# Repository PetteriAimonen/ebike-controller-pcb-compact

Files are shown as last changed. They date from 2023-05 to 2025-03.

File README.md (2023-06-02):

Custom E-bike controller based on VESC 4.10
===========================================

Customized version of [Benjamin Vedder's VESC](https://github.com/vedderb/bldc-hardware) for driving BLDC motors.

VESC Hardware is licensed under the Creative Commons Attribution-ShareAlike 4.0 International License. To view a copy of this license, visit http://creativecommons.org/licenses/by-sa/4.0/.

Can use either VESC firmware or my [custom firmware](https://github.com/PetteriAimonen/ebike-controller/).

Changes:

* Added screw terminals for power cables and 2.54 mm pin headers for signals.
* Most parts are on single-side, with parts available on JLCPCB.
* Added LSM6DS3 accelerometer on board for controlling assist power
* Designed for max. 20A 50V operation.

[Schematic](design/images/BLDC_4.pdf)

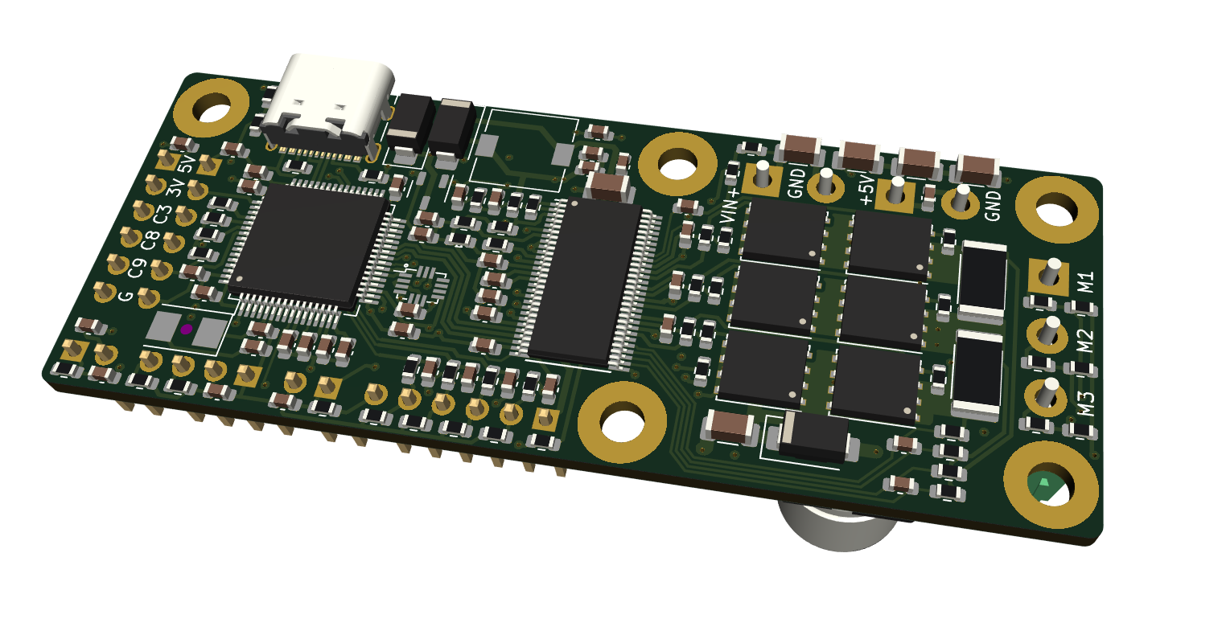
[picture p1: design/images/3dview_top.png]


Designed to mount on an aluminum block for cooling the FETs.
Alternatively a heatsink can be screwed on.

Assembly costs for 5 pcs at JLCPCB as of 2023:

    PCB (with 1 oz inner layer copper and lead-free HASL): $28.00
    Setup fee:$7.88
    Stencil:$1.48
    Components:$97.77
    Extended components fee:$29.56
    SMT Assembly:$3.43

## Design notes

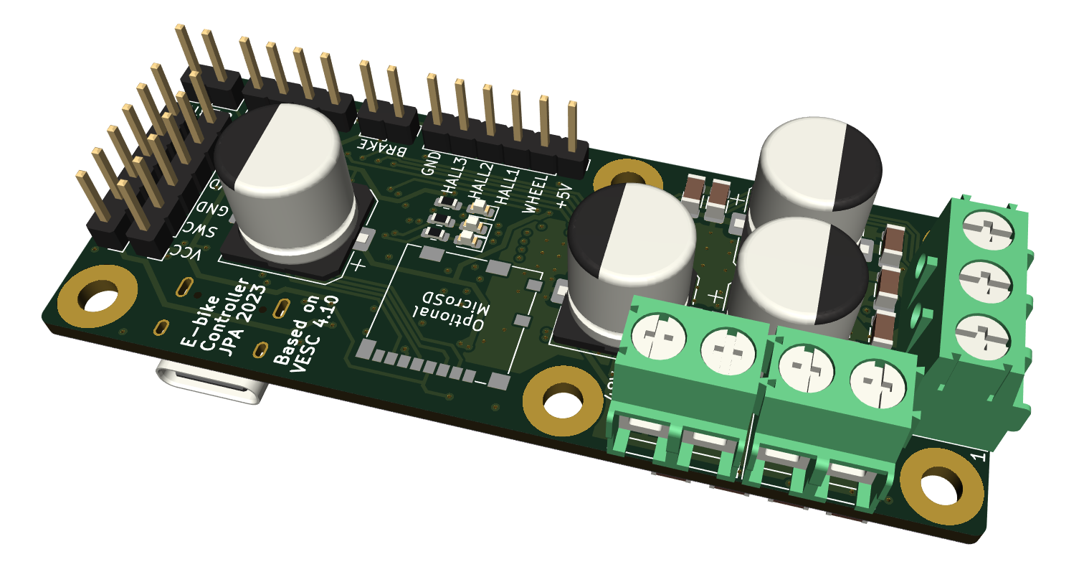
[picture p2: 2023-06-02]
design/images/3dview_bottom.png

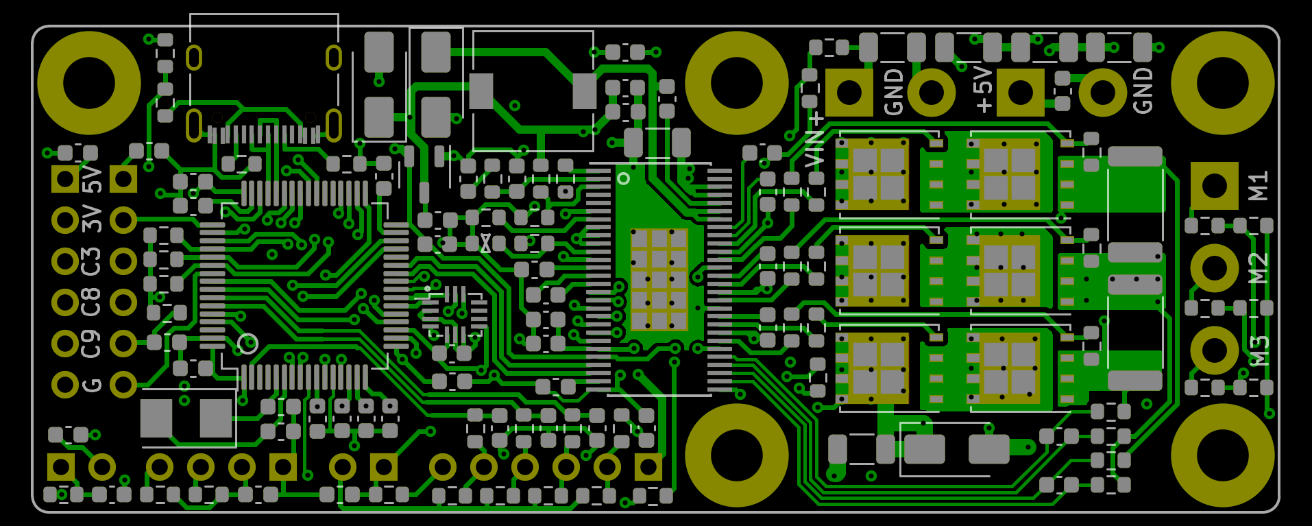
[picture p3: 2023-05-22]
design/images/BLDC_4_top.png

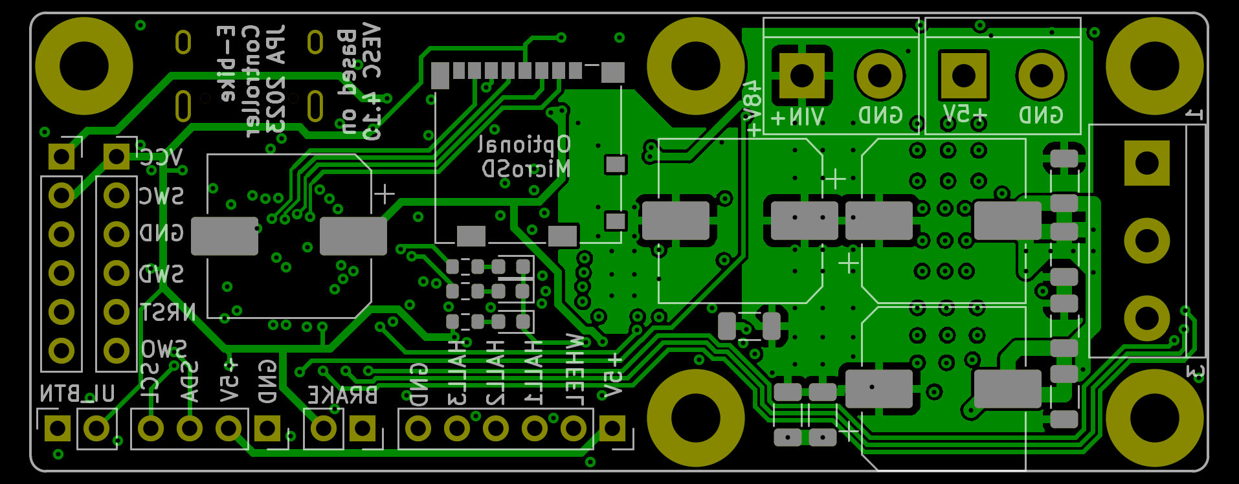
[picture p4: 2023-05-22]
design/images/BLDC_4_bottom.png

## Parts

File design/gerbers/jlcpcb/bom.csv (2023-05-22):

Comment | Designator | Footprint | LCSC
HALL/Encoder | P1 | Connector_PinHeader_2.54mm:PinHeader_1x06_P2.54mm_Vertical | N/A
100nF | C2,C11,C12,C13,C22,C27,C28,C29,C30,C32,C41,C42,C45,C62 | Capacitor_SMD:C_0603_1608Metric | C14663
2k2 | R4,R7,R11,R12,R13,R14,R15,R16,R18,R22,R24,R27,R31,R33 | Resistor_SMD:R_0603_1608Metric | C4190
39k | R3,R23,R26,R30,R32,R36,R46 | Resistor_SMD:R_0603_1608Metric | C23153
5m | R53,R54 | Resistor_SMD:R_2512_6332Metric | C5154719
100R | R37,R38,R48,R49,R50,R51 | Resistor_SMD:R_0603_1608Metric | C22775
RED | D2 | LED_SMD:LED_0603_1608Metric | N/A
GREEN | D1 | LED_SMD:LED_0603_1608Metric | N/A
LED | D3 | LED_SMD:LED_0603_1608Metric | N/A
40V_IN | J3 | TerminalBlock:TerminalBlock_bornier-2_P5.08mm | N/A
100uF,63V | C57,C58,C59 | Capacitor_SMD:CP_Elec_10x10.5 | N/A
Motor | J1 | TerminalBlock:TerminalBlock_bornier-3_P5.08mm | N/A
5V_OUT | J2 | TerminalBlock:TerminalBlock_bornier-2_P5.08mm | N/A
Schottky | D4 | Diode_SMD:D_SMA | C14996
DRV8302 | U3 | Package_SO:HTSSOP-56-1EP_6.1x14mm_P0.5mm_EP3.61x6.35mm | C84672
22u | L1 | Inductor_SMD:L_7.3x7.3_H4.5 | C2839926
470µF | C33 | Capacitor_SMD:CP_Elec_10x10.5 | N/A
4.7uF | C1,C3,C8,C16,C17,C18,C20,C23,C24,C26,C46,C47,C48,C52,C60,C61 | Capacitor_SMD:C_0603_1608Metric | C19666
10k | R2,R19,R20,R44 | Resistor_SMD:R_0603_1608Metric | C25804
220k | R21 | Resistor_SMD:R_0603_1608Metric | C22961
12k | R17 | Resistor_SMD:R_0603_1608Metric | C22790
4.7nF | C4,C5,C6,C7,C21,C34,C36,C501,C502,C503 | Capacitor_SMD:C_0603_1608Metric | C53987
22pF | C15,C19,C38 | Capacitor_SMD:C_0603_1608Metric | C1653
1uF,100V | C9,C37,C39,C40,C43,C44,C49,C50,C51,C53,C54,C55,C56 | Capacitor_SMD:C_1206_3216Metric | C354362
XC6206PxxxMR | U6 | Package_TO_SOT_SMD:SOT-23-3 | C5446
SMAJ48 | D7 | Diode_SMD:D_SMA | C151245
SMAJ5 | D5 | Diode_SMD:D_SMA | C2925443
STM32F40X_LQFP64 | U1 | Package_QFP:LQFP-64_10x10mm_P0.5mm | C15742
SWD | P2 | Connector_PinHeader_2.54mm:PinHeader_1x06_P2.54mm_Vertical | N/A
OLED | P11 | Connector_PinHeader_2.54mm:PinHeader_1x04_P2.54mm_Vertical | N/A
BRAKE | P12 | Connector_PinHeader_2.54mm:PinHeader_1x02_P2.54mm_Vertical | N/A
BUTTONS | P13 | Connector_PinHeader_2.54mm:PinHeader_1x02_P2.54mm_Vertical | N/A
EXTENSION | P14 | Connector_PinHeader_2.54mm:PinHeader_1x06_P2.54mm_Vertical | N/A
MICROSD | U5 | Connector_Card:microSD_HC_Molex_104031-0811 | N/A
LSM6DS3 | U4 | LSM6DS3:LSM6DS3 | C967633
4k7 | R6,R8,R9,R10,R39,R40,R41,R401,R402,R403,R404,R405 | Resistor_SMD:R_0603_1608Metric | C23162
USB_C_Receptacle_USB2.0 | J401 | Connector_USB:USB_C_Receptacle_XKB_U262-16XN-4BVC11 | C319148
8MHz | Y1 | Crystal:Crystal_SMD_5032-2Pin_5.0x3.2mm | C115962
BSC030N08NS5 | Q1,Q2,Q3,Q4,Q5,Q6 | Package_TO_SOT_SMD:TDSON-8-1 | C501507
4R7 | R28,R29,R34,R35,R42,R43 | Resistor_SMD:R_0603_1608Metric | C23164
NTC 10k | R1 | Resistor_SMD:R_0603_1608Metric | C162670

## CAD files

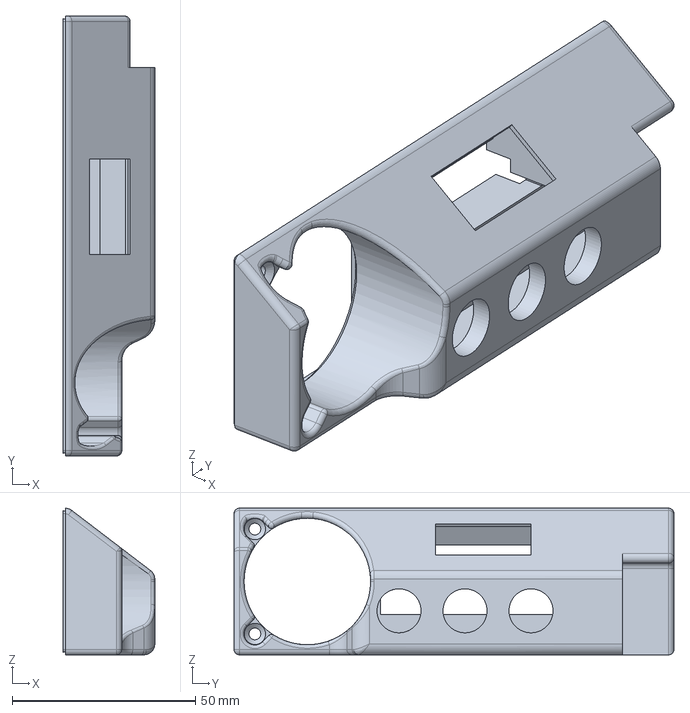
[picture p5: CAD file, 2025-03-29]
mechanics/ui_panel_v3.FCStd
25.0 x 120.0 x 40.0 mm

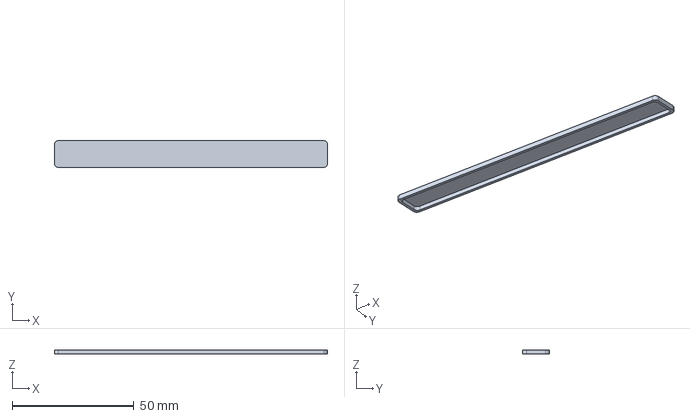
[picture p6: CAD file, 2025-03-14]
mechanics/ledstrip_cover.FCStd
112.0 x 10.9 x 1.70 mm

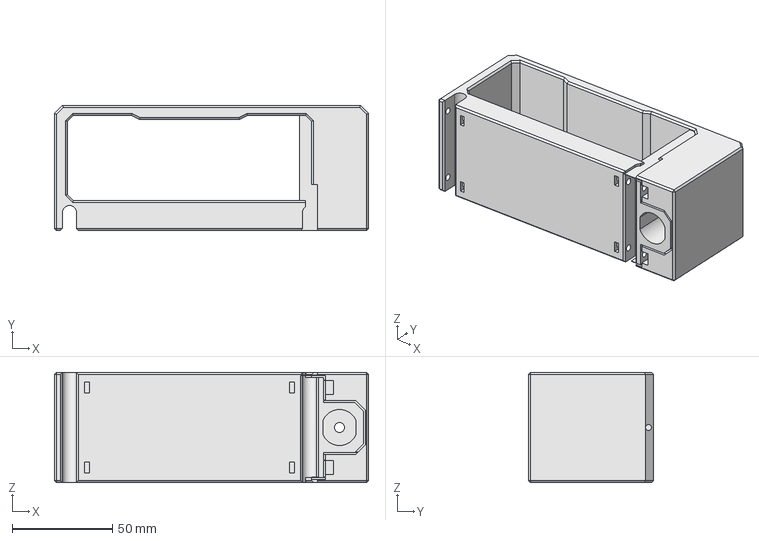
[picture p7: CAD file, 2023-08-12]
mechanics/battery_holder_2.FCStd
157.0 x 62.5 x 55.0 mm

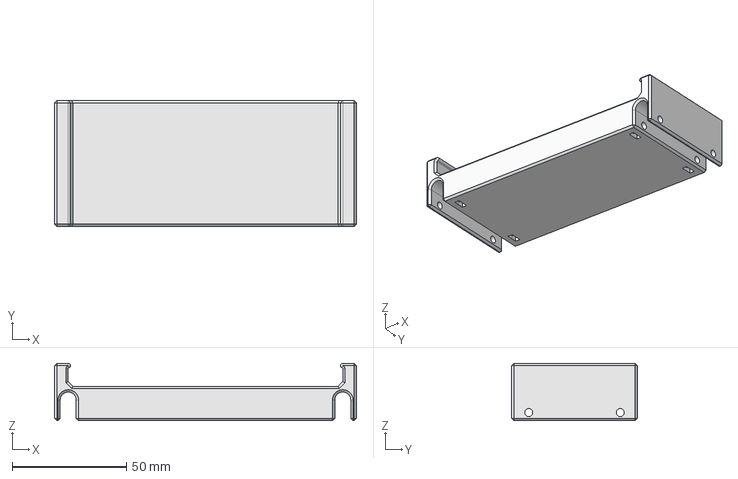
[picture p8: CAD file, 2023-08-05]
mechanics/battery_holder_1.FCStd
132.0 x 55.0 x 25.0 mm

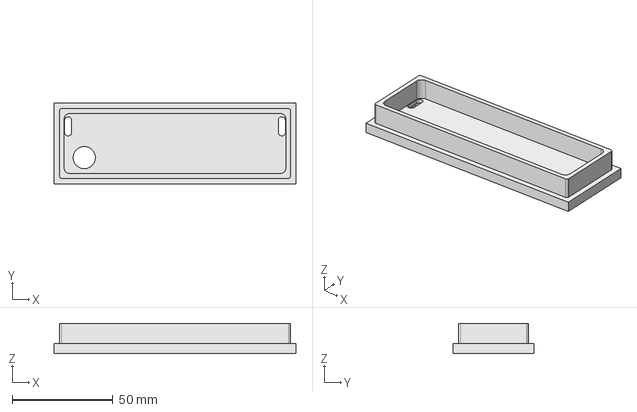
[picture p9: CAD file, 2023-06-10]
mechanics/brakelight_endplate.FCStd
120.0 x 40.0 x 15.0 mm

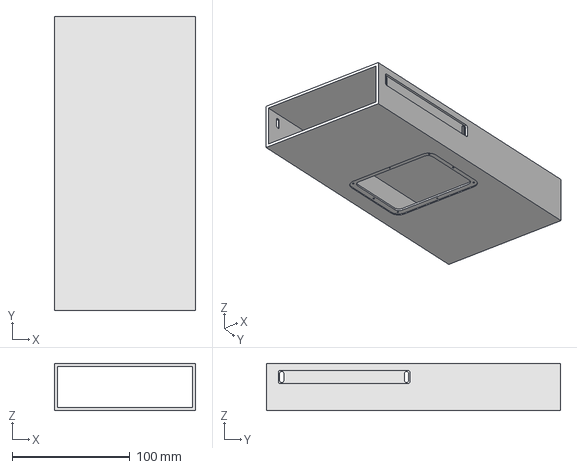
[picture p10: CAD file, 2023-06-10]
mechanics/profile_pipe.FCStd
120.0 x 250.0 x 40.0 mm

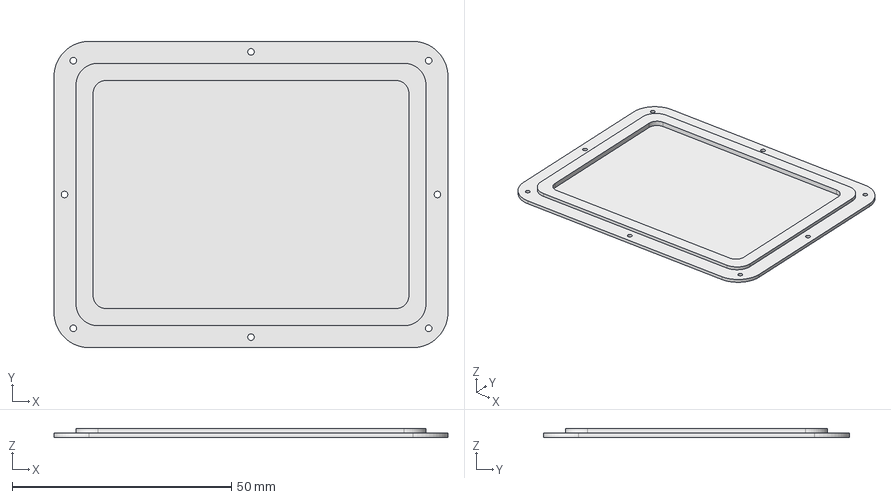
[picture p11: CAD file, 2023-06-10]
mechanics/bms_lid.FCStd
89.8 x 69.8 x 2.00 mm

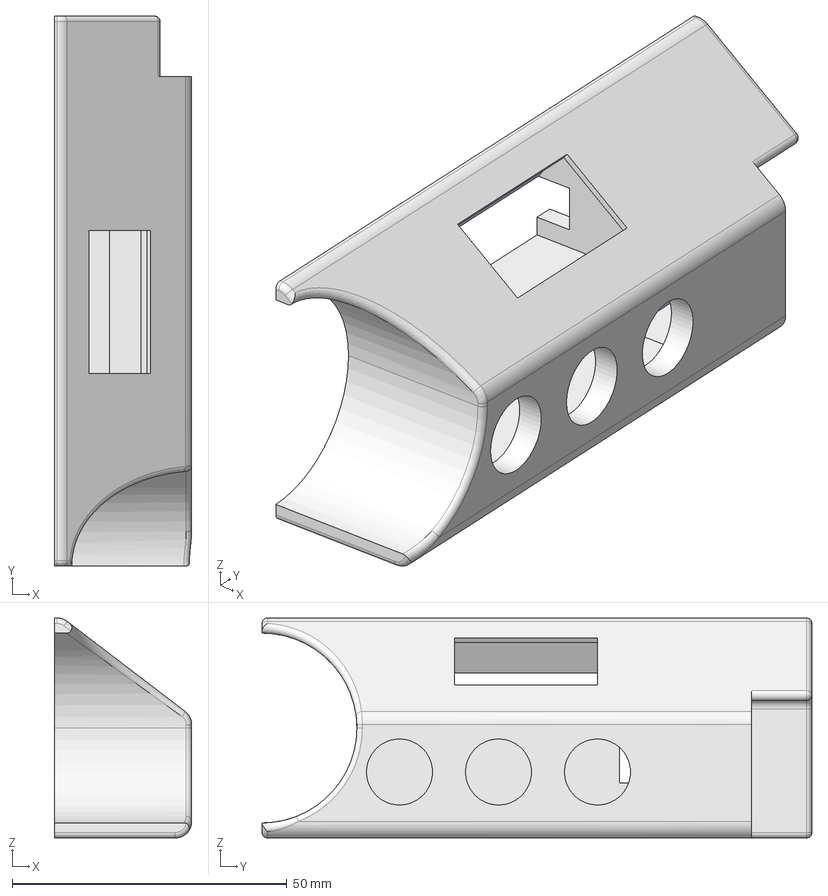
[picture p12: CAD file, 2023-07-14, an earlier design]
mechanics/ui_panel.FCStd
25.0 x 100.0 x 40.0 mm

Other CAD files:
mechanics/assembly.FCStd
mechanics/pcb_holder_endplate.FCStd
mechanics/battery_holder_1.stl
mechanics/battery_holder_2.stl
mechanics/ui_panel.stl
mechanics/ui_panel_v3.stl

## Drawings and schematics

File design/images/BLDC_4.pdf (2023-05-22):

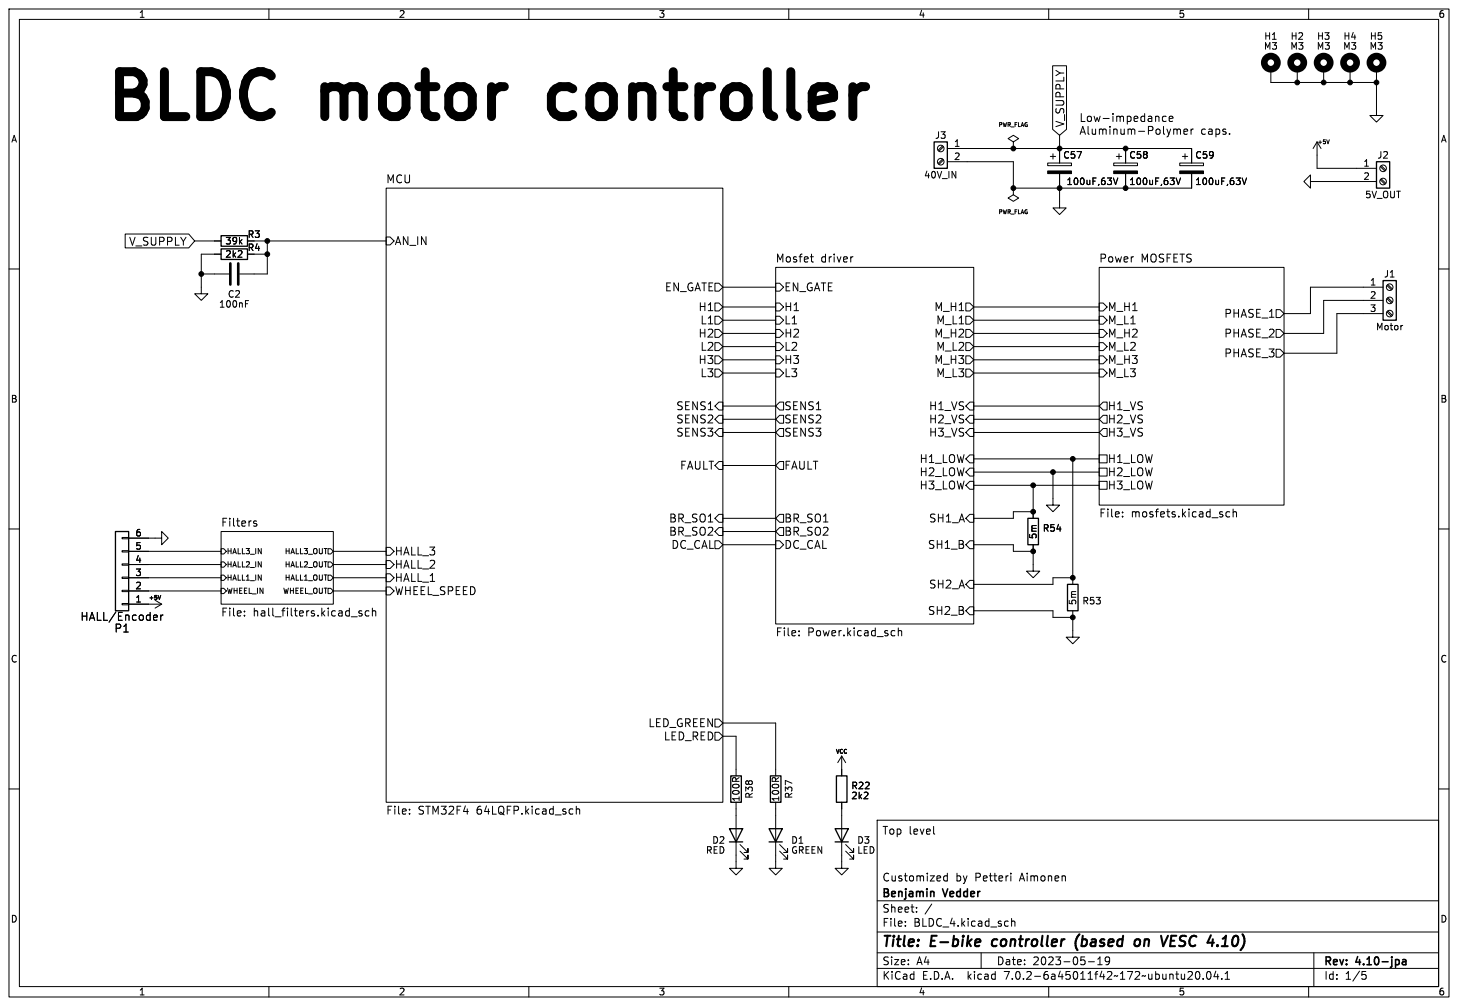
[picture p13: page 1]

Low-impedance BLDC motor controller

SH2_B Mosfet driver File: Power.kicad_sch
L1 FAULT H3 H2 H1 SENS3

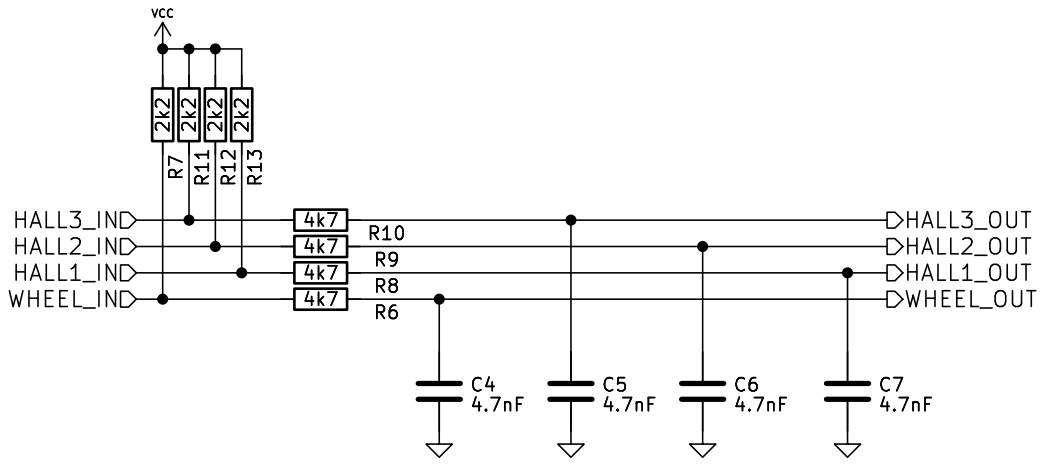
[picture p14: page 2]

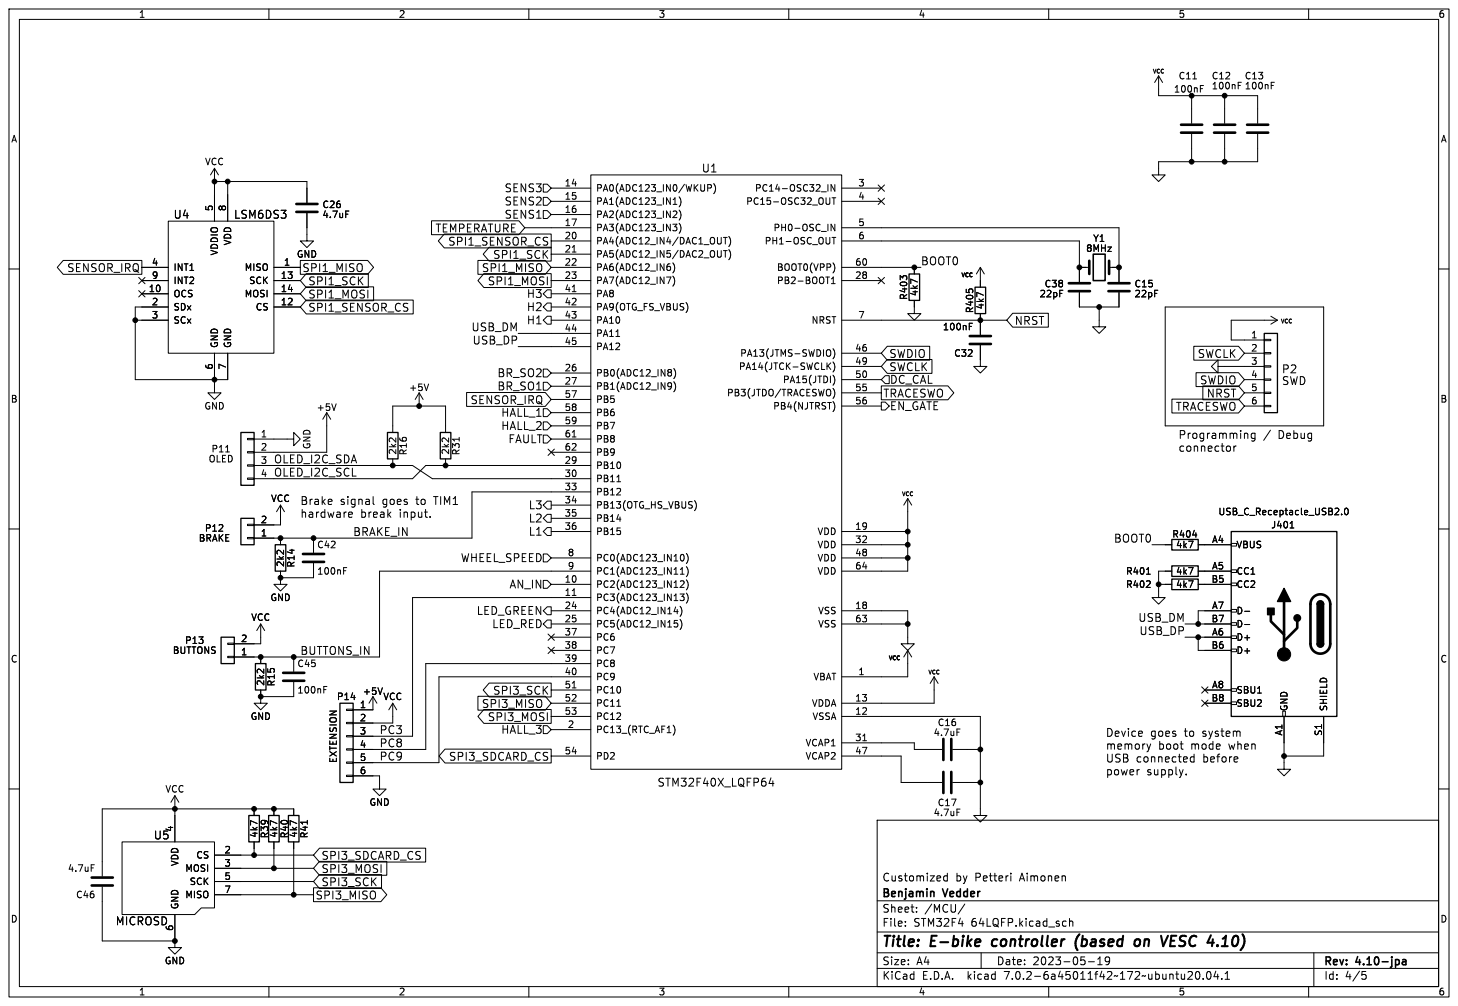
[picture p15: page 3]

connector Brake signal goes to TIM1

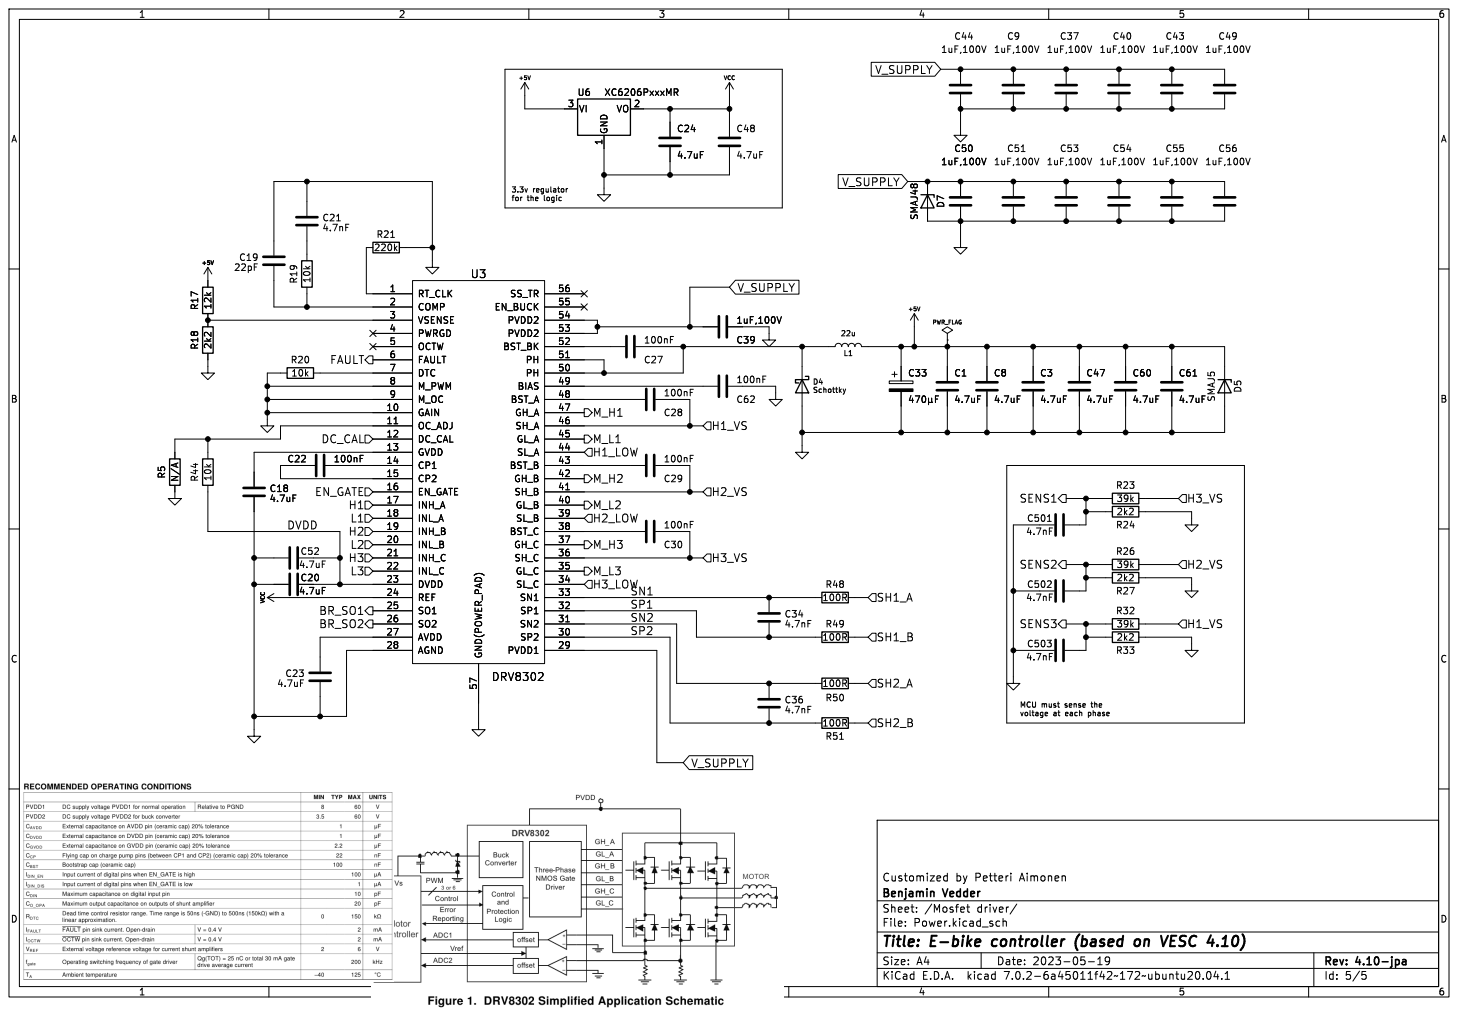
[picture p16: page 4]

MCU must sense the
voltage at each phase

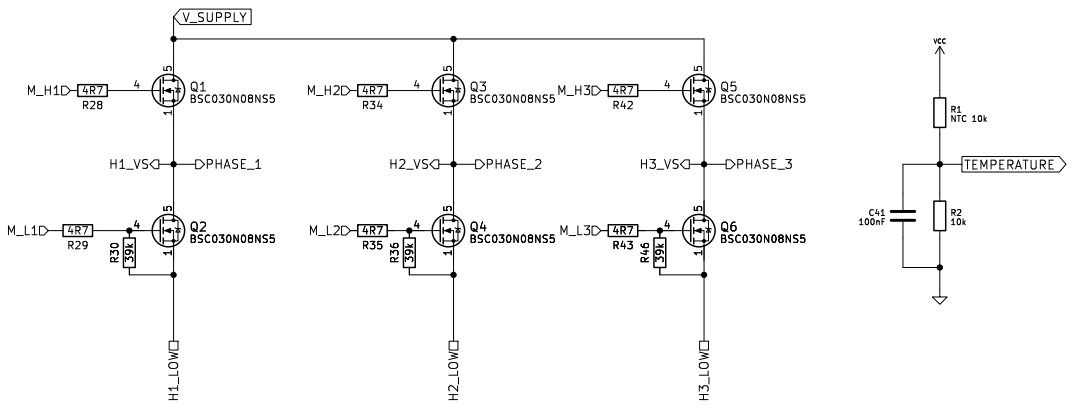
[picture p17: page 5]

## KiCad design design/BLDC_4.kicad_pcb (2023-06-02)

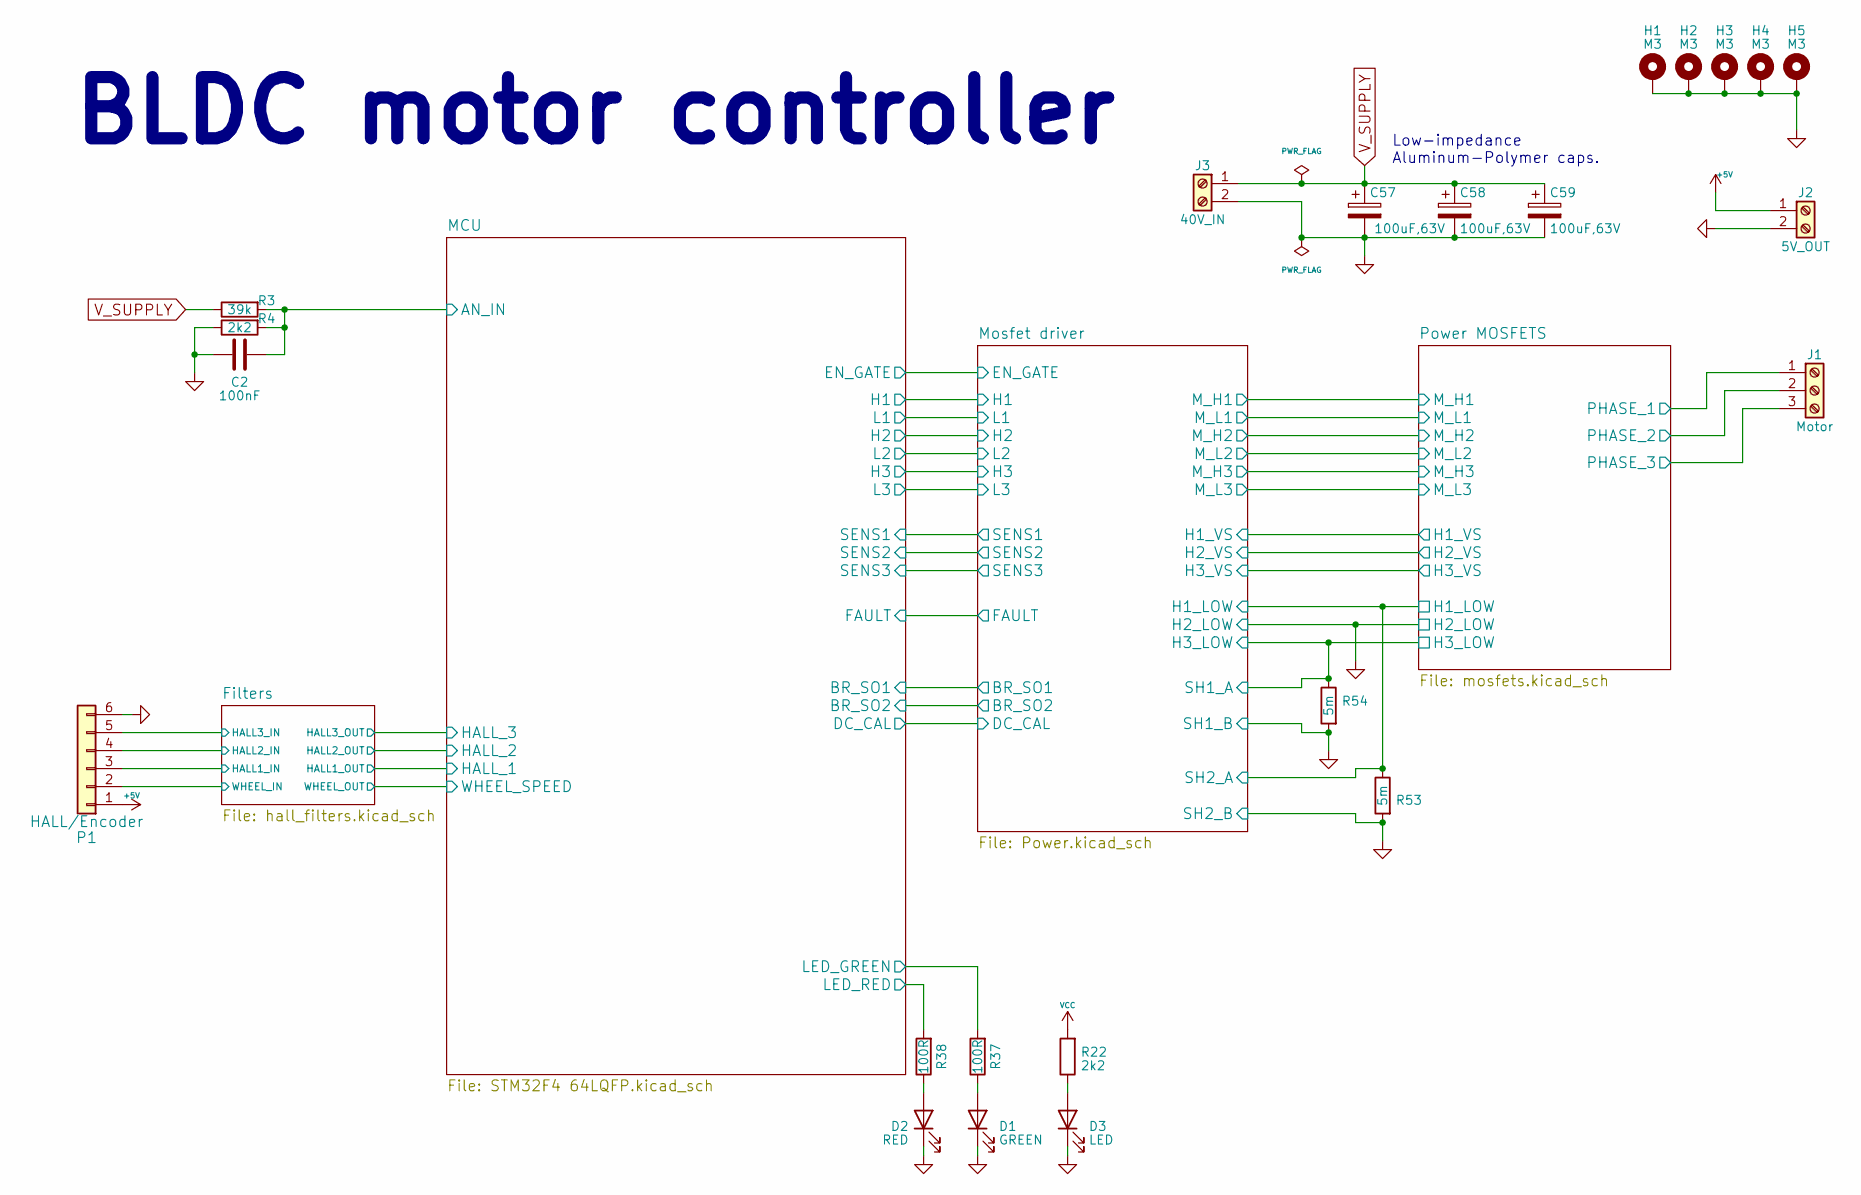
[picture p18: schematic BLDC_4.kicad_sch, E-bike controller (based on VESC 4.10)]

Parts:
C2: 100nF; C_0603_1608Metric; JLCPCB C14663
C57, C58, C59: 100uF,63V; CP_Elec_10x10.5; JLCPCB N/A
D1: GREEN; LED_0603_1608Metric; JLCPCB N/A
D2: RED; LED_0603_1608Metric; JLCPCB N/A
D3: LED; LED_0603_1608Metric; JLCPCB N/A
H1, H2, H3, H4, H5: M3; MountingHole_3.2mm_M3_Pad; JLCPCB N/A
J1: Motor; TerminalBlock_bornier-3_P5.08mm; JLCPCB N/A
J2: 5V_OUT; TerminalBlock_bornier-2_P5.08mm; JLCPCB N/A
J3: 40V_IN; TerminalBlock_bornier-2_P5.08mm; JLCPCB N/A
P1: HALL/Encoder; PinHeader_1x06_P2.54mm_Vertical; JLCPCB N/A
R3: 39k; R_0603_1608Metric; JLCPCB C23153
R4, R22: 2k2; R_0603_1608Metric; JLCPCB C4190
R37, R38: 100R; R_0603_1608Metric; JLCPCB C22775
R53, R54: 5m; R_2512_6332Metric; JLCPCB C5154719

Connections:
+5V: J2.1, P1.1; also elsewhere on the board
/Filters/HALL1_IN: P1.3; also elsewhere on the board
/Filters/HALL2_IN: P1.4; also elsewhere on the board
/Filters/HALL3_IN: P1.5; also elsewhere on the board
/Filters/WHEEL_IN: P1.2; also elsewhere on the board
/MCU/AN_IN: C2.2, R3.2, R4.2; also elsewhere on the board
/MCU/LED_GREEN: R37.2; also elsewhere on the board
/MCU/LED_RED: R38.2; also elsewhere on the board
/Mosfet driver/H1_LOW: R53.1; also elsewhere on the board
/Mosfet driver/H1_VS: J1.1; also elsewhere on the board
/Mosfet driver/H2_VS: J1.2; also elsewhere on the board
/Mosfet driver/H3_LOW: R54.1; also elsewhere on the board
/Mosfet driver/H3_VS: J1.3; also elsewhere on the board
GND: C2.1, C57.2, C58.2, C59.2, D1.1 (K), D2.1 (K), D3.1 (K), H1.1, H2.1, H3.1, H4.1, H5.1, J2.2, J3.2, P1.6, R4.1, R53.2, R54.2; also elsewhere on the board
unnamed: D1.2 (A), R37.1
unnamed: D2.2 (A), R38.1
unnamed: D3.2 (A), R22.1
VCC: R22.2; also elsewhere on the board
V_SUPPLY: C57.1, C58.1, C59.1, J3.1, R3.1; also elsewhere on the board

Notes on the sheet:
Low-impedance Aluminum-Polymer caps.
BLDC motor controller

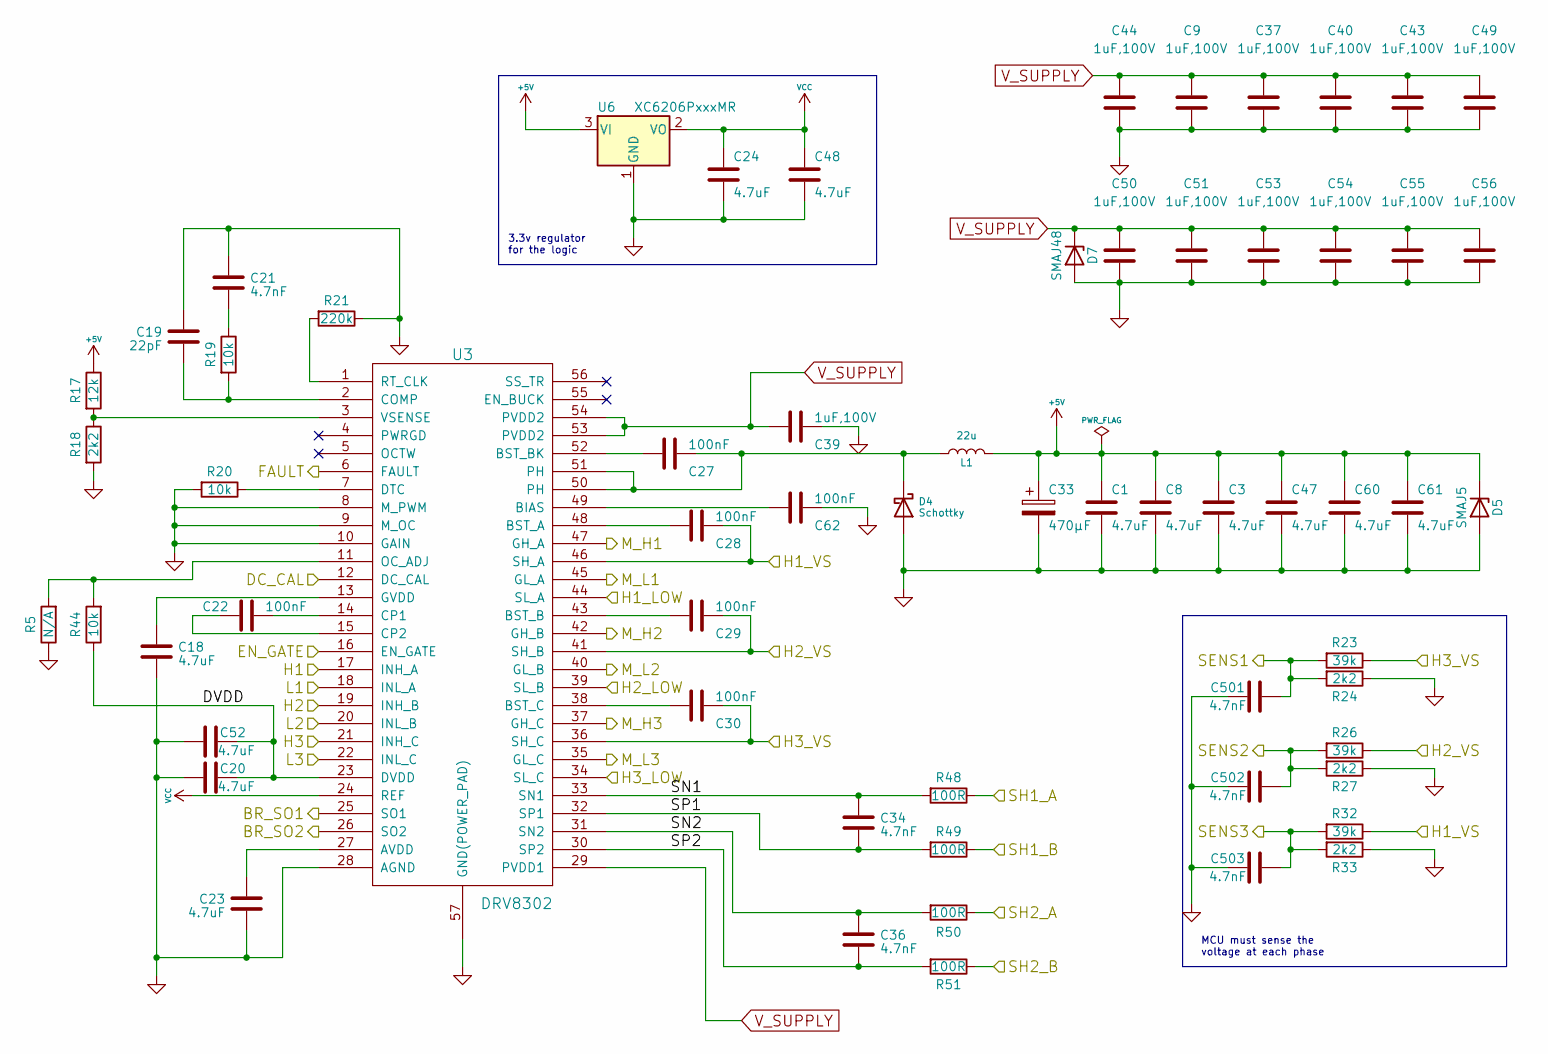
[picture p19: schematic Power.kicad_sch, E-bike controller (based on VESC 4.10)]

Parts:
C1, C3, C8, C18, C20, C23, C24, C47, C48, C52, C60, C61: 4.7uF; C_0603_1608Metric; JLCPCB C19666
C9, C37, C39, C40, C43, C44, C49, C50, C51, C53, C54, C55, C56: 1uF,100V; C_1206_3216Metric; JLCPCB C354362
C19: 22pF; C_0603_1608Metric; JLCPCB C1653
C21, C34, C36, C501, C502, C503: 4.7nF; C_0603_1608Metric; JLCPCB C53987
C22, C27, C28, C29, C30, C62: 100nF; C_0603_1608Metric; JLCPCB C14663
C33: 470µF; CP_Elec_10x10.5; JLCPCB N/A
D4: Schottky; D_SMA; JLCPCB C14996
D5: SMAJ5; D_SMA; JLCPCB C2925443
D7: SMAJ48; D_SMA; JLCPCB C151245
L1: 22u; L_7.3x7.3_H4.5; JLCPCB C2839926
R5: N/A; R_0603_1608Metric; JLCPCB N/A
R17: 12k; R_0603_1608Metric; JLCPCB C22790
R18, R24, R27, R33: 2k2; R_0603_1608Metric; JLCPCB C4190
R19, R20, R44: 10k; R_0603_1608Metric; JLCPCB C25804
R21: 220k; R_0603_1608Metric; JLCPCB C22961
R23, R26, R32: 39k; R_0603_1608Metric; JLCPCB C23153
R48, R49, R50, R51: 100R; R_0603_1608Metric; JLCPCB C22775
U3: DRV8302; HTSSOP-56-1EP_6.1x14mm_P0.5mm_EP3.61x6.35mm; JLCPCB C84672
U6: XC6206PxxxMR; SOT-23-3; JLCPCB C5446

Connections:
+5V: C1.1, C3.1, C8.1, C33.1, C47.1, C60.1, C61.1, D5.1 (K), L1.2, R17.1, U6.3 (VI); also elsewhere on the board
/MCU/BR_SO1: U3.25 (SO1); also elsewhere on the board
/MCU/BR_SO2: U3.26 (SO2); also elsewhere on the board
/MCU/DC_CAL: U3.12 (DC_CAL); also elsewhere on the board
/MCU/EN_GATE: U3.16 (EN_GATE); also elsewhere on the board
/MCU/FAULT: U3.6 (FAULT); also elsewhere on the board
/MCU/H1: U3.17 (INH_A); also elsewhere on the board
/MCU/H2: U3.19 (INH_B); also elsewhere on the board
/MCU/H3: U3.21 (INH_C); also elsewhere on the board
/MCU/L1: U3.18 (INL_A); also elsewhere on the board
/MCU/L2: U3.20 (INL_B); also elsewhere on the board
/MCU/L3: U3.22 (INL_C); also elsewhere on the board
/MCU/SENS1: C501.2, R23.2, R24.2; also elsewhere on the board
/MCU/SENS2: C502.2, R26.2, R27.2; also elsewhere on the board
/MCU/SENS3: C503.2, R32.2, R33.2; also elsewhere on the board
/Mosfet driver/DVDD: C20.2, C52.2, R44.1, U3.23 (DVDD)
/Mosfet driver/H1_LOW: R50.1, U3.44 (SL_A); also elsewhere on the board
/Mosfet driver/H1_VS: C28.1, R32.1, U3.46 (SH_A); also elsewhere on the board
/Mosfet driver/H2_VS: C29.1, R26.1, U3.41 (SH_B); also elsewhere on the board
/Mosfet driver/H3_LOW: R48.1, U3.34 (SL_C); also elsewhere on the board
/Mosfet driver/H3_VS: C30.1, R23.1, U3.36 (SH_C); also elsewhere on the board
/Mosfet driver/M_H1: U3.47 (GH_A); also elsewhere on the board
/Mosfet driver/M_H2: U3.42 (GH_B); also elsewhere on the board
/Mosfet driver/M_H3: U3.37 (GH_C); also elsewhere on the board
/Mosfet driver/M_L1: U3.45 (GL_A); also elsewhere on the board
/Mosfet driver/M_L2: U3.40 (GL_B); also elsewhere on the board
/Mosfet driver/M_L3: U3.35 (GL_C); also elsewhere on the board
/Mosfet driver/SN1: C34.1, R48.2, U3.33 (SN1)
/Mosfet driver/SN2: C36.1, R50.2, U3.31 (SN2)
/Mosfet driver/SP1: C34.2, R49.2, U3.32 (SP1)
/Mosfet driver/SP2: C36.2, R51.2, U3.30 (SP2)
GND: C1.2, C3.2, C8.2, C9.2, C18.2, C19.1, C20.1, C21.1, C23.1, C24.2, C33.2, C37.2, C39.1, C40.2, C43.2, C44.2, C47.2, C48.2, C49.2, C50.2, C51.2, C52.1, C53.2, C54.2, C55.2, C56.2, C60.2, C61.2, C62.1, C501.1, C502.1, C503.1, D4.2 (A), D5.2 (A), D7.2 (A), R5.1, R18.2, R20.2, R21.1, R24.1, R27.1, R33.1, R49.1, R51.1, U3.8 (M_PWM), U3.9 (M_OC), U3.10 (GAIN), U3.28 (AGND), U3.39 (SL_B), U3.57 (GND(POWER_PAD)), U6.1 (GND); also elsewhere on the board
unnamed: C21.2, R19.1
unnamed: C27.1, D4.1 (K), L1.1, U3.50 (PH), U3.51 (PH)
unnamed: C23.2, U3.27 (AVDD)
unnamed: C62.2, U3.49 (BIAS)
unnamed: C28.2, U3.48 (BST_A)
unnamed: C29.2, U3.43 (BST_B)
unnamed: C27.2, U3.52 (BST_BK)
unnamed: C30.2, U3.38 (BST_C)
unnamed: C19.2, R19.2, U3.2 (COMP)
unnamed: C22.1, U3.14 (CP1)
unnamed: C22.2, U3.15 (CP2)
unnamed: R20.1, U3.7 (DTC)
unnamed: C18.1, U3.13 (GVDD)
unnamed: R5.2, R44.2, U3.11 (OC_ADJ)
unnamed: R21.2, U3.1 (RT_CLK)
unnamed: R17.2, R18.1, U3.3 (VSENSE)
VCC: C24.1, C48.1, U3.24 (REF), U6.2 (VO); also elsewhere on the board
V_SUPPLY: C9.1, C37.1, C39.2, C40.1, C43.1, C44.1, C49.1, C50.1, C51.1, C53.1, C54.1, C55.1, C56.1, D7.1 (K), U3.29 (PVDD1), U3.53 (PVDD2), U3.54 (PVDD2); also elsewhere on the board

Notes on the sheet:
MCU must sense the voltage at each phase
3.3v regulator for the logic

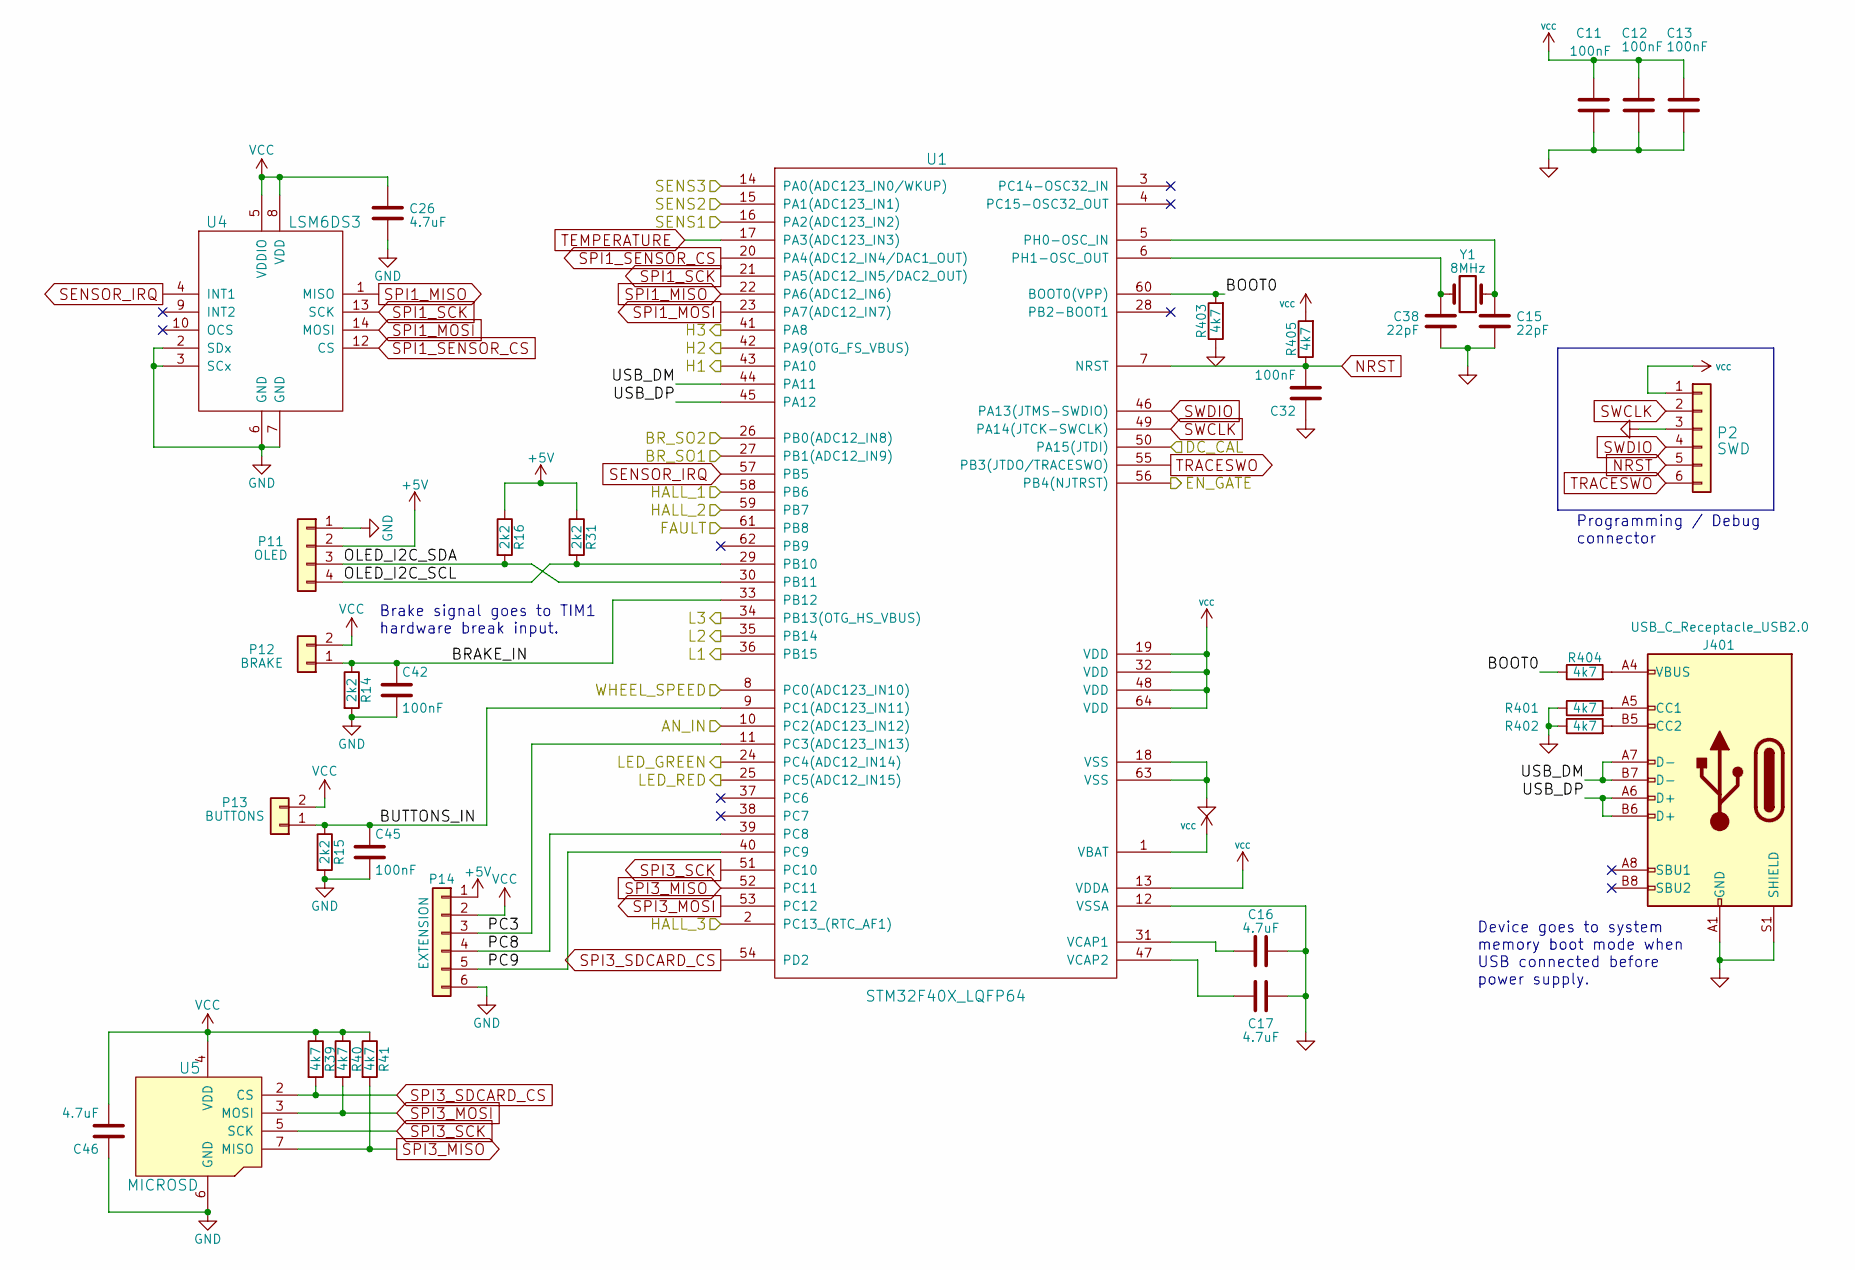
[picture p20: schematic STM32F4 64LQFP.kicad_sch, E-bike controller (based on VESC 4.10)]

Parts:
C11, C12, C13, C32, C42, C45: 100nF; C_0603_1608Metric; JLCPCB C14663
C15, C38: 22pF; C_0603_1608Metric; JLCPCB C1653
C16, C17, C26, C46: 4.7uF; C_0603_1608Metric; JLCPCB C19666
J401: USB_C_Receptacle_USB2.0; USB_C_Receptacle_XKB_U262-16XN-4BVC11; JLCPCB C319148
P2: SWD; PinHeader_1x06_P2.54mm_Vertical; JLCPCB N/A
P11: OLED; PinHeader_1x04_P2.54mm_Vertical; JLCPCB N/A
P12: BRAKE; PinHeader_1x02_P2.54mm_Vertical; JLCPCB N/A
P13: BUTTONS; PinHeader_1x02_P2.54mm_Vertical; JLCPCB N/A
P14: EXTENSION; PinHeader_1x06_P2.54mm_Vertical; JLCPCB N/A
R14, R15, R16, R31: 2k2; R_0603_1608Metric; JLCPCB C4190
R39, R40, R41, R401, R402, R403, R404, R405: 4k7; R_0603_1608Metric; JLCPCB C23162
U1: STM32F40X_LQFP64; LQFP-64_10x10mm_P0.5mm; JLCPCB C15742
U4: LSM6DS3; JLCPCB C967633
U5: MICROSD; microSD_HC_Molex_104031-0811; JLCPCB N/A
Y1: 8MHz; Crystal_SMD_5032-2Pin_5.0x3.2mm; JLCPCB C115962

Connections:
+5V: P11.2, P14.1, R16.1, R31.1; also elsewhere on the board
/Filters/HALL1_OUT: U1.58 (PB6); also elsewhere on the board
/Filters/HALL2_OUT: U1.59 (PB7); also elsewhere on the board
/Filters/HALL3_OUT: U1.2 (PC13_(RTC_AF1)); also elsewhere on the board
/Filters/WHEEL_OUT: U1.8 (PC0(ADC123_IN10)); also elsewhere on the board
/MCU/AN_IN: U1.10 (PC2(ADC123_IN12)); also elsewhere on the board
/MCU/BOOT0: R403.2, R404.1, U1.60 (BOOT0(VPP))
/MCU/BRAKE_IN: C42.1, P12.1, R14.1, U1.33 (PB12)
/MCU/BR_SO1: U1.27 (PB1(ADC12_IN9)); also elsewhere on the board
/MCU/BR_SO2: U1.26 (PB0(ADC12_IN8)); also elsewhere on the board
/MCU/BUTTONS_IN: C45.1, P13.1, R15.1, U1.9 (PC1(ADC123_IN11))
/MCU/DC_CAL: U1.50 (PA15(JTDI)); also elsewhere on the board
/MCU/EN_GATE: U1.56 (PB4(NJTRST)); also elsewhere on the board
/MCU/FAULT: U1.61 (PB8); also elsewhere on the board
/MCU/H1: U1.43 (PA10); also elsewhere on the board
/MCU/H2: U1.42 (PA9(OTG_FS_VBUS)); also elsewhere on the board
/MCU/H3: U1.41 (PA8); also elsewhere on the board
/MCU/L1: U1.36 (PB15); also elsewhere on the board
/MCU/L2: U1.35 (PB14); also elsewhere on the board
/MCU/L3: U1.34 (PB13(OTG_HS_VBUS)); also elsewhere on the board
/MCU/LED_GREEN: U1.24 (PC4(ADC12_IN14)); also elsewhere on the board
/MCU/LED_RED: U1.25 (PC5(ADC12_IN15)); also elsewhere on the board
/MCU/OLED_I2C_SCL: P11.4, R31.2, U1.29 (PB10)
/MCU/OLED_I2C_SDA: P11.3, R16.2, U1.30 (PB11)
/MCU/PC3: P14.3, U1.11 (PC3(ADC123_IN13))
/MCU/PC8: P14.4, U1.39 (PC8)
/MCU/PC9: P14.5, U1.40 (PC9)
/MCU/SENS1: U1.16 (PA2(ADC123_IN2)); also elsewhere on the board
/MCU/SENS2: U1.15 (PA1(ADC123_IN1)); also elsewhere on the board
/MCU/SENS3: U1.14 (PA0(ADC123_IN0/WKUP)); also elsewhere on the board
/MCU/USB_DM: J401.A7 (D-), J401.B7 (D-), U1.44 (PA11)
/MCU/USB_DP: J401.A6 (D+), J401.B6 (D+), U1.45 (PA12)
GND: C11.1, C12.1, C13.1, C15.2, C16.2, C17.2, C26.1, C32.1, C38.2, C42.2, C45.2, C46.1, J401.A1 (GND), J401.A12 (GND), J401.B1 (GND), J401.B12 (GND), J401.S1 (SHIELD), P2.3, P11.1, P14.6, R14.2, R15.2, R401.1, R402.1, R403.1, U1.12 (VSSA), U1.18 (VSS), U1.63 (VSS), U4.2 (SDx), U4.3 (SCx), U4.6 (GND), U4.7 (GND), U5.6 (GND); also elsewhere on the board
NRST: C32.2, P2.5, R405.1, U1.7 (NRST)
unnamed: J401.A5 (CC1), R401.2
unnamed: J401.B5 (CC2), R402.2
unnamed: J401.A4 (VBUS), J401.A9 (VBUS), J401.B4 (VBUS), J401.B9 (VBUS), R404.2
unnamed: C15.1, U1.5 (PH0-OSC_IN), Y1.1
unnamed: C38.1, U1.6 (PH1-OSC_OUT), Y1.2
unnamed: C16.1, U1.31 (VCAP1)
unnamed: C17.1, U1.47 (VCAP2)
SENSOR_IRQ: U1.57 (PB5), U4.4 (INT1)
SPI1_MISO: U1.22 (PA6(ADC12_IN6)), U4.1 (MISO)
SPI1_MOSI: U1.23 (PA7(ADC12_IN7)), U4.14 (MOSI)
SPI1_SCK: U1.21 (PA5(ADC12_IN5/DAC2_OUT)), U4.13 (SCK)
SPI1_SENSOR_CS: U1.20 (PA4(ADC12_IN4/DAC1_OUT)), U4.12 (CS)
SPI3_MISO: R41.2, U1.52 (PC11), U5.7 (MISO)
SPI3_MOSI: R40.2, U1.53 (PC12), U5.3 (MOSI)
SPI3_SCK: U1.51 (PC10), U5.5 (SCK)
SPI3_SDCARD_CS: R39.2, U1.54 (PD2), U5.2 (CS)
SWCLK: P2.2, U1.49 (PA14(JTCK-SWCLK))
SWDIO: P2.4, U1.46 (PA13(JTMS-SWDIO))
TEMPERATURE: U1.17 (PA3(ADC123_IN3)); also elsewhere on the board
TRACESWO: P2.6, U1.55 (PB3(JTDO/TRACESWO))
VCC: C11.2, C12.2, C13.2, C26.2, C46.2, P2.1, P12.2, P13.2, P14.2, R39.1, R40.1, R41.1, R405.2, U1.1 (VBAT), U1.13 (VDDA), U1.19 (VDD), U1.32 (VDD), U1.48 (VDD), U1.64 (VDD), U4.5 (VDDIO), U4.8 (VDD), U5.4 (VDD); also elsewhere on the board

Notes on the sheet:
Brake signal goes to TIM1 hardware break input.
Programming / Debug connector
Device goes to system memory boot mode when USB connected before power supply.

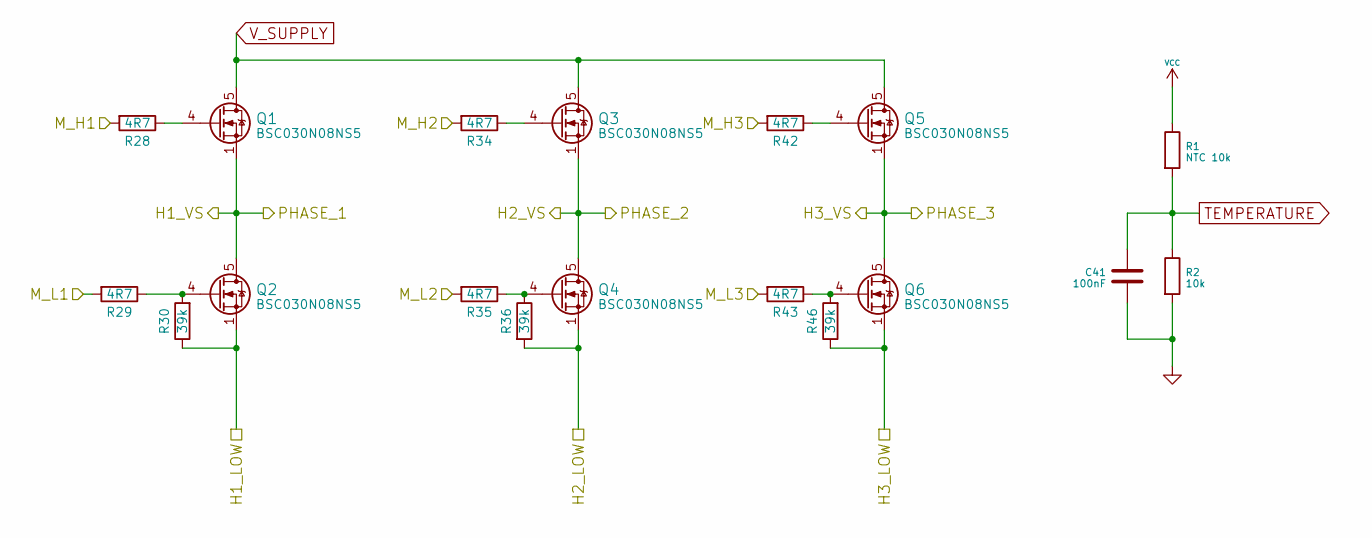
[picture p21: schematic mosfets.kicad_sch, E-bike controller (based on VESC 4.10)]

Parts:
C41: 100nF; C_0603_1608Metric; JLCPCB C14663
Q1, Q2, Q3, Q4, Q5, Q6: BSC030N08NS5; TDSON-8-1; JLCPCB C501507
R1: NTC 10k; R_0603_1608Metric; JLCPCB C162670
R2: 10k; R_0603_1608Metric; JLCPCB C25804
R28, R29, R34, R35, R42, R43: 4R7; R_0603_1608Metric; JLCPCB C23164
R30, R36, R46: 39k; R_0603_1608Metric; JLCPCB C23153

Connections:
/Mosfet driver/H1_LOW: Q2.1 (S), Q2.2 (S), Q2.3 (S), R30.1; also elsewhere on the board
/Mosfet driver/H1_VS: Q1.1 (S), Q1.2 (S), Q1.3 (S), Q2.5 (D); also elsewhere on the board
/Mosfet driver/H2_VS: Q3.1 (S), Q3.2 (S), Q3.3 (S), Q4.5 (D); also elsewhere on the board
/Mosfet driver/H3_LOW: Q6.1 (S), Q6.2 (S), Q6.3 (S), R46.1; also elsewhere on the board
/Mosfet driver/H3_VS: Q5.1 (S), Q5.2 (S), Q5.3 (S), Q6.5 (D); also elsewhere on the board
/Mosfet driver/M_H1: R28.2; also elsewhere on the board
/Mosfet driver/M_H2: R34.2; also elsewhere on the board
/Mosfet driver/M_H3: R42.2; also elsewhere on the board
/Mosfet driver/M_L1: R29.2; also elsewhere on the board
/Mosfet driver/M_L2: R35.2; also elsewhere on the board
/Mosfet driver/M_L3: R43.2; also elsewhere on the board
GND: C41.2, Q4.1 (S), Q4.2 (S), Q4.3 (S), R2.2, R36.2; also elsewhere on the board
unnamed: Q1.4 (G), R28.1
unnamed: Q2.4 (G), R29.1, R30.2
unnamed: Q3.4 (G), R34.1
unnamed: Q4.4 (G), R35.1, R36.1
unnamed: Q5.4 (G), R42.1
unnamed: Q6.4 (G), R43.1, R46.2
TEMPERATURE: C41.1, R1.2, R2.1; also elsewhere on the board
VCC: R1.1; also elsewhere on the board
V_SUPPLY: Q1.5 (D), Q3.5 (D), Q5.5 (D); also elsewhere on the board

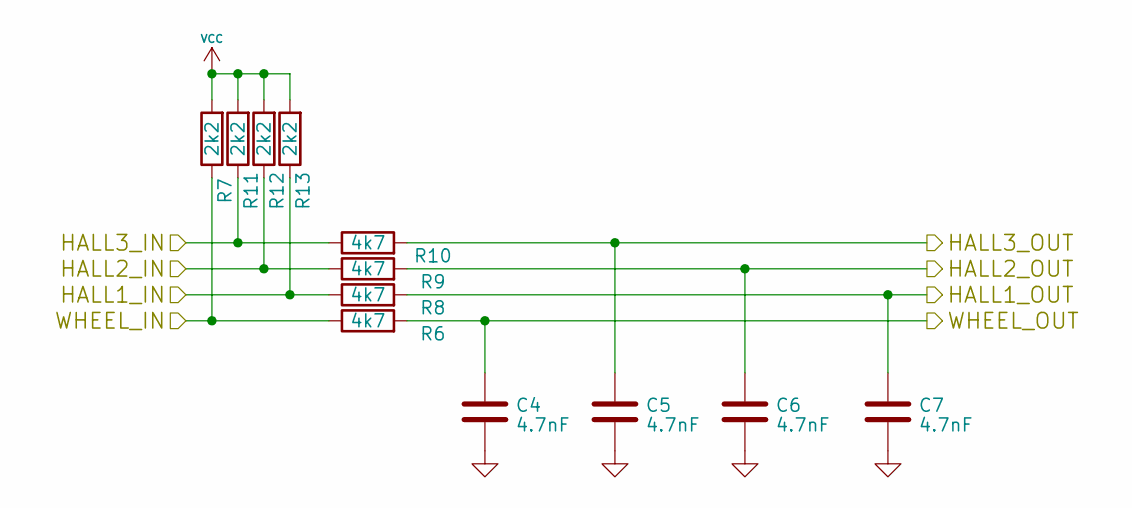
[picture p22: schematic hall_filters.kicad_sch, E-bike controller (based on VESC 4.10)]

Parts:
C4, C5, C6, C7: 4.7nF; C_0603_1608Metric; JLCPCB C53987
R6, R8, R9, R10: 4k7; R_0603_1608Metric; JLCPCB C23162
R7, R11, R12, R13: 2k2; R_0603_1608Metric; JLCPCB C4190

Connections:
/Filters/HALL1_IN: R8.1, R13.1; also elsewhere on the board
/Filters/HALL1_OUT: C7.1, R8.2; also elsewhere on the board
/Filters/HALL2_IN: R9.1, R12.1; also elsewhere on the board
/Filters/HALL2_OUT: C6.1, R9.2; also elsewhere on the board
/Filters/HALL3_IN: R10.1, R11.1; also elsewhere on the board
/Filters/HALL3_OUT: C5.1, R10.2; also elsewhere on the board
/Filters/WHEEL_IN: R6.1, R7.1; also elsewhere on the board
/Filters/WHEEL_OUT: C4.2, R6.2; also elsewhere on the board
GND: C4.1, C5.2, C6.2, C7.2; also elsewhere on the board
VCC: R7.2, R11.2, R12.2, R13.2; also elsewhere on the board

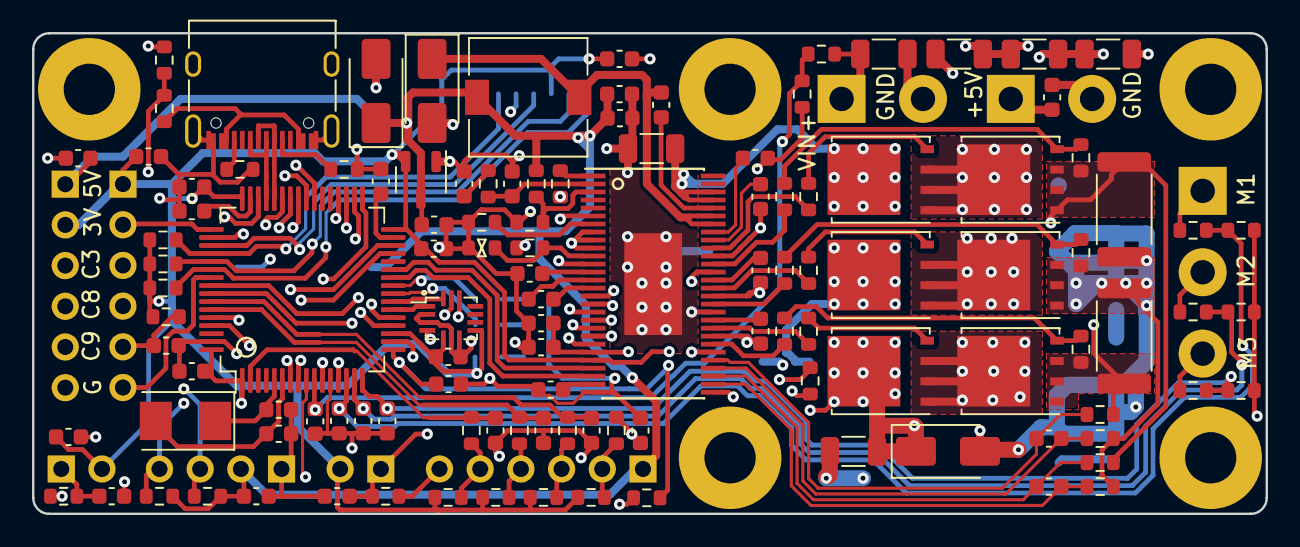
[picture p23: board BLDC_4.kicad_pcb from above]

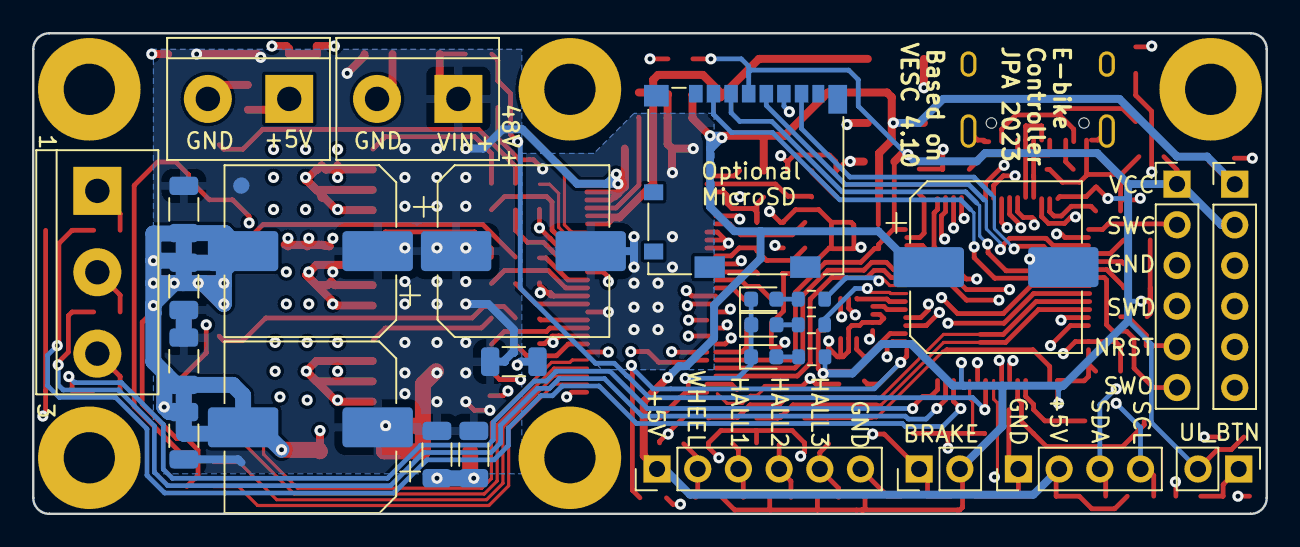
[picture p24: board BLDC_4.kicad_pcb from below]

Board: 4 copper layers, 77.0 x 30.0 mm, 149 parts (27 on the bottom side), 101 nets.

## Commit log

2015-10-25 Add 60V->5V buck converter and bypassing caps on board
    [BLDC_4.sch, CAN.sch, Power.sch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]
2015-11-01 schema mods done
    [BLDC_4.kicad_pcb, BLDC_4.sch, Power.sch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]
2023-05-22 Relayout to more compact version, update to KiCad 7
    [BLDC4.10_BOM.ods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]
2023-06-02 Update README, add FreeCAD design of mounting
    [BLDC_4.kicad_pcb, pcb_holder_endplate.FCStd]
2023-06-10 More mechanical parts
    [assembly.FCStd, bms_lid.FCStd, brakelight_endplate.FCStd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]
2023-07-14 Mechanical parts
    [ui_panel.FCStd, ui_panel.stl]
2023-08-05 Battery holder bracket
    [battery_holder_1.FCStd, battery_holder_1.stl]
2023-08-12 battery locking bracket
    [battery_holder_2.FCStd, battery_holder_2.stl]
2025-03-14 ledstrip cover
    [ledstrip_cover.FCStd]
2025-03-28 Slight adjustment of UI panel design
    [ui_panel_v3.FCStd, ui_panel_v3.stl]
2025-03-29 Fix geometry
    [ui_panel_v3.FCStd, ui_panel_v3.stl]
